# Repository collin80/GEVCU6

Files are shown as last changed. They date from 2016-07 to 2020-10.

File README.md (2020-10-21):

GEVCU
=====

Generalized Electric Vehicle Control Unit

Our website can be found at : http://www.evtv.me

NOTE: This branch is quite old and not really supported at this point. Use the DEV branch of this project if at all possible. It is newer and better supported. Eventually the DEV branch will be merged back into this master branch.

A project to create a fairly Arduino compatible ECU firmware
to interface with various electric vehicle hardware over CANbus
(and possibly other comm channels)

The project now builds in the Arduino IDE. So, use it to compile, send the firmware to the GEVCU hardware, and monitor serial. It all works very nicely.

You will need the following to have any hope of compiling and running the firmware:
- A GEVCU board. This version supports hardware 6.23c and later.
- Arduino IDE 1.5.4 - or later
- due_can library - There is a repo for this under github.com/Collin80
- can_common library - Also under Collin80 repos
- due_rtc library - Also under Collin80
- due_wire library - once again
- DueTimer library - and again
- Microsmooth library (Also in repos: https://github.com/collin80/Microsmooth)
- Adafruit_BLE_SPI library - You need the development branch from my repos: https://github.com/collin80/Adafruit_BLE_SPI/tree/development

All libraries belong in %USERPROFILE%\Documents\Arduino\libraries (Windows) or ~/Arduino/libraries (Linux/Mac).
You will need to remove -master or any other postfixes. Your library folders should be named as above.

The canbus is supposed to be terminated on both ends of the bus. If you are testing with a DMOC and GEVCU then you've got two devices, each on opposing ends of the bus. GEVCU hardware is already terminated internally.

This software is MIT licensed:

Copyright (c) 2014 Collin Kidder, Michael Neuweiler, Charles Galpin, Jack Rickard

Permission is hereby granted, free of charge, to any person obtaining
a copy of this software and associated documentation files (the
"Software"), to deal in the Software without restriction, including
without limitation the rights to use, copy, modify, merge, publish,
distribute, sublicense, and/or sell copies of the Software, and to
permit persons to whom the Software is furnished to do so, subject to
the following conditions:

The above copyright notice and this permission notice shall be included
in all copies or substantial portions of the Software.

THE SOFTWARE IS PROVIDED "AS IS", WITHOUT WARRANTY OF ANY KIND,
EXPRESS OR IMPLIED, INCLUDING BUT NOT LIMITED TO THE WARRANTIES OF
MERCHANTABILITY, FITNESS FOR A PARTICULAR PURPOSE AND NONINFRINGEMENT.
IN NO EVENT SHALL THE AUTHORS OR COPYRIGHT HOLDERS BE LIABLE FOR ANY
CLAIM, DAMAGES OR OTHER LIABILITY, WHETHER IN AN ACTION OF CONTRACT,
TORT OR OTHERWISE, ARISING FROM, OUT OF OR IN CONNECTION WITH THE
SOFTWARE OR THE USE OR OTHER DEALINGS IN THE SOFTWARE.

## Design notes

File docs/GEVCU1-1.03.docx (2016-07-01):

GENERALIZED ELECTRIC VEHICLE CONTROL UNIT

GEVCU

SPECIFICATION

Jack Rickard jack@evtv.me

# BACKGROUND

For 40 years and more, individual tinkerers and innovators have been modifying existing automobiles to electric drive and often building electrically powered vehicles from scratch.

The early “controllers” that evolved to replace simple switching and resistive controls to control the speed of the driver motors were mostly pulse width modulated (PWM) devices to provide an averaged DC signal to a series DC motor. These simple chopper voltage control devices were generally referred to as “controllers” and translated driver input from “controls” such as the accelerator pedal, ignition switch, and brake to this motor driving voltage to control its speed and direction – and consequently the vehicle.

There are of course many other types of motors such as separately excited DC motors, brushless DC motors, permanent magnet motors and AC induction motors. Most of these polyphase motors required 3 phase “inverters” to convert the DC power of the battery pack into three phase drive signals varying the voltage and frequency of the power to the motor to accomplish the same thing.

Most of the DC “controllers” received the inputs directly by wiring from the sensors or controls in the cars.

In recent years, among automobile manufacturers, the use of the Controller Area Network bus protocol has been adopted for many of the items in the automobile, including the internal combustion engine – often called an Engine Control Unit or a Vehicle Control Unit which forms the central “brains” of the car. It is connected to various sensors and controls by wire but communicates to other subsystems of the vehicle such as the instrumentation, ABS system, transmission, environmental system using this CANbus as the common link.

Automakers have eschewed the DC motor in favor of either permanent magnet AC motors or AC induction motors. And the “inverters” developed to drive these were interfaced to this same CANbus model for control input.

Because of the varying nature of the cars, the ECU or VCU would be specifically designed for that vehicle. But the Inverters driving AC motors can be somewhat generalized to work in any car by using CANbus to control them.

The VCU would be specifically designed and software specifically written for that vehicle. This was hardcoded into flash memory and defined the operation of the vehicle. No end user input or options were provided. Firmware updates were accomplished by revising the hard code, recompiling, and having the controller reflashed with the new binaries at the dealership during normal maintenance.

And so thousands of these VCUs could be flashed when built, with the software specific to that particular vehicle.

The VCU would of course be completely inappropriate and non functional in another vehicle make or model.

As many automakers are experimenting with product introductions of plug-in electric vehicles and hybrid gasoline/electric vehicles, many of the components used in these vehicles are becoming available when the cars are salvaged and are recycled through salvage yards and such online services as eBay.

As such, they will become a resource to individual tinkerers and those converting existing cars to electric drive.

But almost all of these components were designed to be controlled by the Vehicle Control Unit that came with the original car.

It would be a serious advantage, to have a more generalized vehicle control unit that allowed some basic configuration allowing these conversions to modify operation of the VCU to accommodate THEIR car without the need to entirely rewrite the software and flash the VCU.

As almost all VCU accomplish the same basic functions, a simple configuration input that does not involve assembly language or C programming to change it would be of substantial utility.

This document describes the design of a Generalized Vehicle Control Unit. The multicontroller hardware will allow connection of the basic sensor set necessary to drive the car such as throttle signals, brake signals, ignition signal, and control the basic common outputs such as brake lights, fuel level, rpm, power usage, while serving in the central role of converting these inputs to CAN messages for the inverter to actually drive the car.

The operation of this device can be modified, within fairly narrow constraints, by a simple configuration “menu” style input that non-programmers can access and make changes to, in order to interface the VCU to the particular car they want to convert.

The initial immediate need for this Generalized Vehicle Control Unit was the acquisition of a significant number of Siemens 1PV5135-4WS14-Z motors and Digital Motor Control (DMOC) 645 units from the liquidation of Azure Dynamics Corporation by EVtv.

This DMOC no longer has control inputs, but is rather designed to respond to CANbus commands solely.

The intent in developing this GEVCU, is to not only allow access to a number of OEM hardware components, but also to transfer the product support function faced by the manufacturers and developers of the Inverter Power Electronics to the GEVCU.

In theory, CANbus message digests for ANY motor inverter could be easily patched into the GEVCU to allow operation of that power inverter without ANY support from the developer of the power electronics.

This should quickly allow the developers of power electronics inverters to provide this equipment to individuals at the same or comparable prices as they do to the OEM automakers, without having to incur additional expense to train and support those users in the use of the product. Training and use becomes a function of using the GEVCU itself.

# HARDWARE DESIGN PHILOSOPHY

GEVCU developers can use any hardware they can build or locate that accommodates the basic sensor inputs and instrumentation outputs described in this document. OPEN SOURCE hardware prototype equipment is preferred for GEVCU development and the software should be designed to operate on an open source prototype system. But it is perfectly acceptable to then design custom hardware from that reference design to reduce costs and eliminate extraneous unused components available in the open source prototype system design.

The hardware must provide:

1. At least one CANbus port capable of CAN 1.0 and 2.0b operation, including both 11 bit and 29 bit identifiers.
2. A sufficient number of analog to digital converter inputs of sufficient resolution to accommodate the sensor inputs described in this document. Vehicle sensors are overwhelmingly based on 0-5V architectures. And so these A/D inputs must accept signals in the 0-5v range, and the device must be able to provide 5v supplies to those sensors in sufficient power levels to not alter the 5v reference level when all such sensors are connected.
3. Digital inputs capable of recognizing on/off signals from the vehicle given in 12v and ground states. Active can be either of active high 12v or active low gnd but active high is the normally preferred method as 12v is normally the enabling signal for other systems such as brake lights.
4. Relay driver outputs. Digital outputs suitable for engaging relays, contactors, and other relay like devices in the vehicle.
5. PWM outputs. Sufficient PWM outputs to drive legacy instrumentation such as tachometers and fuel gages as described in this document.
6. ETHERNET port. It is very important for the end user to be able to modify the operation of this device (configure it) without the need for unique external software programs running on specific operating systems. The user should be able to easily configure this device using any device with an Ethernet connection and an http browser. It is actually completely acceptable to also provide means of configuration using a browser via 802.b/g/n wireless, Bluetooth, or Universal Serial Bus (USB) interfaces.

The overall requirement here is that no special type of computer, operation system, or unique configuration software external to the GEVCU can be required to easily modify GEVCU configuration and operation.

Additionally we seek to AVOID the additional expense in the device of a dedicated display and input devices in the GEVCU hardware itself. Once configured, this hardware would be entirely redundant. Configuration is conceivably a one time or perhaps very infrequent event.

7. Processor power sufficient to perform the GEVCU tasks without delay in vehicle operation or control. This is quite important as many systems shut down without regular updated CAN messages to keep them alive and the results of any inability to make schedule could be catastrophic in a moving vehicle.
8. Popularity and user base. When selecting hardware, recognize the advantage of popular and widely adopted devices with large user base. That user base provides a level of additional support and utility that it forms a serious element of the ultimate value of the GEVCU.
9. Tool chain. Strong preference should be given to devices with simple and free compilers such as the Arduino IDE. An open hardware open software device makes little sense if it requires a $2800 compiler environment to make code changes.

# SOFTWARE DESIGN PHILOSOPHY

The basic software design philosophy is to be an open source, object oriented software design. This is to accommodate a couple of needs for the GEVCU

1. Ability to add contributions from any external source or user that prove effective in practice. Anyone should be able to read, modify, recompile and run the original source code to the GEVCU. As such, it should be open source and use inexpensive or free, widely available tool chains to compile. If they are caught in the act of doing something useful, that improvement can be added to the main trunk of the software development.
2. Ability to add support for additional inverters. Almost all of the available inverters accomplish essentially the same functions and provide essentially the same information. But the specific CAN bus IDs, command structure and data formats vary entirely from one inverter to another.

The GEVCU will be initially developed to support the Azure Dynamics DMOC645 inverter. But the ability to add the specific CAN bus message commands for other inverters, without having to make changes to the main program structure in a modular fashion is very important.

Make a strong effort to isolate the inverter object from the rest of the code, with an eye towards allowing the use of other inverter objects with no changes to the non-inverter object code.

3. Object Oriented C++ code is an obvious choice. Assembly language subroutines where desirable or advantageous are perfectly acceptable.
4. Recognize an inevitable desire to add additional functions to this device quite beyond the initial GEVCU spec. The GEVCU, by virtue of it’s central role in vehicle operation, would be the natural place to go for controlling electrically powered air conditioner compressors, CANbus controlled battery chargers, CANbus controlled Electronic Power Assisted Steering units (EPAS) etc.

# COMPLIANCE

For teams developing GEVCU hardware and/or software, it should be noted that compliance with this specification is ENTIRELY voluntary.

That said, there is a slight motivator you might want to take into consideration. I happen to know that software developers are notoriously averse to actually documenting anything and hardware designers are even worse – they not only don’t document but they can’t remember either. They’ll have to get with Charlie and get back to you later.

On the other hand, if you design TO the GEVCU specification, and when making necessary changes NOT in compliance get those changes incorporated BACK into the spec, you will find an odd resemblance between your newly finished product and my upcoming best selling novel :

# INSTALLATION AND OPERATION OF THE GENERALIZED ELECTRIC VEHICLE CONTROL UNIT.

By Jack Rickard.

See the movie at a theatre near you. Coming this summer.

# PART 1 - INPUTS

# THROTTLE

The throttle or accelerator is undoubtedly the central control input for a controller. This is how we vary the power output of the inverter to the motor, and thus motor speed and torque, and consequently vehicle speed.

There are two broad types of throttles that must be accommodated: legacy throttles and modern dual signal drive by wire throttles found in currently manufactured vehicles.

The legacy throttle most widely used is a simple 5kohm potentiometer linked to a mechanical pedal usually by wire. The controller provides 5v and a reference ground to the two ends of the resistor, and the pickup arm of the potentiometer returns some fraction of that source voltage to the controller as the signal input.

There are also single channel hall-effect throttles available on the market. But their operation is largely identical. 5v and ref gnd is provided to them, and they return some value between 0 and 5v based on position.

Modern drive by wire throttles used in vehicles today use the same 5v and ref gnd input, but they will provide TWO signal inputs to the controller. These are often two signals of different scale: ie. 0.5 to 4.5 and 1.2 to 3.2. Or they might be inverse function where one signal is 1-4v while the other is 4-1v. In some cases they can be both differing in scale and direction.

These throttles are generally designed for safety in that the controller is suppose to compare the two signals, which have a known relationship, and if the two signals do not correspond, the assumption is that one or both are faulty. As a result, the controller reduces all motor torque and speed commands to zero. This prevents a runaway situation resulting from loss of ground, or loss of 5v, or other wiring incident or component failure.

PINS: 1. 5vdc supply voltage 50 ma out to sensor

2. Signal 0-5vdc ADC input ADC

3. Optional sanity check voltage ADC input

3. Reference return – ground out to sensor

CONFIGURATION VARIABLES:

THROTMIN: This parameter sets the minimum voltage where the throttle is considered active. Voltages below this value are read as no throttle input.

Example: 0.80 would indicate 0.80v

THROTMAX: This parameter sets the maximum voltage where the throttle is considered active. Voltages above this value are read as no throttle input.

Example: 4.75 would indicate 4.75v

THROTNOTMIN: This parameter sets the minimum voltage where the optional sanity check throttle input is considered active. Voltages below this value are read as no throttle input.

Example: 1.20 would indicate 1.20v

THROTNOTMAX: This parameter sets the maximum voltage where the optional sanity check throttle input is considered active. Voltages above this value are read as no throttle input.

Example: 3.60 would indicate 3.60v

The sanity check is NOT performed if either THROTNOTMIN or THROTNOTMAX is zero. If they are non zero, the percentage of maximum throttle signal between THROTNOTMIN and THROTNOTMAX is calculated. Also the percentage of maximium throttle signal between THROTMIN and THROTMAX is calculated. The two percentages are compared, and if not within 5% of each other, a fault is thrown and CANbus signals generated to put inverter at zero torque and zerospeed.

Note that this calculation MUST handle the case where THROTNOTMIN is a larger positive voltage value than THROTNOTMAX – the inverse case.

THROTREGEN: Voltages between this value and THROTMIN result in a linear increase in regenerative braking, with maximum regenerative braking established by THROTMAXREGEN at the THROTMIN voltage and essentially 0 percent of MAXREGEN at the THROTREGEN point.

Example: 1.50 indicates 1.50v

Zero regenerative braking at 1.50 v increasing to THROTMAXREGEN at THROTMIN.

In this way, as you begin easing off the throttle through the deadband, at THROTREGEN regenerative braking is still zero. As the voltage falls, regenerative braking INCREASES to the point set by THROTMAXREGEN when the voltage falls to THROTMIN. And so the further we remove the throttle, the greater the amount of regenerative torque is applied.

THROTFWD: Typically a small voltage value above THROTREGEN establishing a “dead band” between the THROTREGEN point and the THROTFWD point.

Example: 1.8v

In this example, from THROTREGEN (1.50v_ to THROTFWD (1.8v) is the deadband or coast zone. NO torque or speed commands are provided to the inverter if throttle input is both valid and in this band, allowing the motor and the vehicle to free roll.

The area between THROTFWD and THROTMAX defines the region of forward acceleration with the minimum torque/speed values occurring at THROTFWD and the maximum torque and speed values at THROTMAX.

THROTMAP: This variable represents a voltage between and THROTMAX where a 50% torque and speed level is defined.

A linear increase of torque and speed is mapped between THROTFWD and THROTMAP with 50% of available torque and speed occurring at THROTMAP.

A linear increase in torque and speed is also mapped between THROTMAP and THROT MAX representing the remaining 50% of available torque.

This entered value is then used to warp the throttle curve. For example:

THROTFWD: 1.80v

THROTMAP: 3.80v

THROTMAX: 4.65v

It can be seen that the first 50% of available torque is mapped between 1.80 and 3.80v while the second 50% of available torque is mapped linearly between 3.80v and 4.65v.

In this way, low speed handling and maneuvering has greater resolution spread across 2.00v of the throttle range, while less resolution is provided across the upper 0.85v. Higher resolution is desired at take off, or while parking, or reversing, while it is generally not needed in going from 50% to full power when we are basically just wanting a big increase in power. THROTMAP can be used to slide this point between those two extremes.

THROTMAXREGEN: This variable defines the percentage of available maximum torque that is available for regenerative braking at the THROTMIN point.

Note that a value of 0 indicates no regenerative braking at all using the throttle.

MAXREGEN: This variable defines the percentage of available maximum torque that is ever available for regenerative braking.

MAXTORQ: This defines the maximum torque available for any purpose.

# BRAKE

You might note that the throttle input also has provisions for regenerative braking. The brake signal does as well. We would assume that the vehicle has a fully functional normal brake system, and that it also has a brake switch used to turn on the brake lights.

Regenerative braking is normally a function of the brake input.

PINS: 1. 5vdc supply voltage 50 ma out to sensor

2. Brake pressure sensor signal 0-5vdc input ADC

3. Reference return – ground out to sensor

4. Brake light input – 0 or 12v digital input

CONFIGURATION VARIABLES:

BRAKEMIN: This parameter sets the minimum voltage where the brake sensor is considered active. Voltages below this value are read as no brake input.

BRAKEMAX: The maximum voltage logic will read as valid brake pressure sensor input. Voltages above BRAKEMAX are read as no brake input.

BRAKEMAXREGEN. This is a value from 0 to 100 representing the percentage of MAXTORQ that can be applied during regenerative braking.

The actual value of regenerative braking during a braking event is a linear value between MAXTHROTREGEN at BRAKEMIN and BRAKEMAXREGEN at BRAKE MAX.

In this way, when you remove your foot from the throttle, the regenerative level is set at the value of MAXTHROTREGEN. When your foot first applies to the brake, that SAME level of REGEN is maintained. As more brake pressure is applied, the regenerative braking torque increases until it reaches BRAKEMAXREGEN at the BRAKEMAX point.

Note that by setting BRAKEMAX to some voltage LESS than the actual maximum voltage provided by the sensor, you can slide the regenerative braking zone toward the very lightest application of brake, and as you continue to press the pedal, regenerative braking ceases and the normal brake system takes over. This can be effective to get maxium regenerative braking effect before the normal disk or drum brakes begin to become effective.

Normally, NO regenerative braking will be provided without a secondary signal from the brake light input. This is a secondary input from a separate source used to enable regenerative braking.

BRAKREGENRAMPTIME. This is a value between 0 and 255 representing the number of hundredths of a second to use to ramp from THROTMAXREGEN to BRAKEMAXREGEN if the brake sensor input value is below BRAKEMIN but the brake light input is active.

In this event, we assume we are NOT USING a brake pressure tranducer input at all. But we do have an active brake light switch signal. The regenerative braking will gradually increase from THROTMAXREGEN to BRAKEMAXREGEN in linear fashion across the entered time value with a max time of 2.5seconds.

This is counterintuitive and we’ve actually seen inverters with this function coded in backwards. But it doesn’t work well when braking.

In the event we are not using regen on the throttle, and want to use it on the brakes, but have no transducer, the regenerative braking will gradually be applied when we step on the brake pedal and steadily increase. If we get too much braking, we simply remove our foot from the brake. Regen goes to zero. We can REAPPLY the brake pedal and again regenerative braking starts to increase. In practice, this feels like you are pumping the brakes.

# REGENERATIVE BRAKING ADJUST

Regenerative braking is a highly subjective “feel” issue. It would be very nice to provide a knob on an electric vehicle where the driver could manually adjust the regen level just by turning the knob.

PINS: 1. 5vdc supply voltage 50 ma out to sensor

2. Regenerative brake adjust signal 0-5vdc input ADC

3. Reference return – ground out to sensor

CONFIGURATION VARIABLES:

REGENSCALE. This variable is set between 0 and 100% based on the voltage read on the regenerative braking adjust signal input. Voltages below 1v set this value to 0. Voltages between 1 and 4v are converted to a decimal value less than 1 indicating the percentage of regen desired. Voltages above 4 are read as 4.

THROTMAXREGEN and BRAKEMAXREGEN are scaled by multiplying the values entered on the configuration screen by REGENSCALE.

As a result, potentiometer settings resulting in an input voltage less than 1 effectively disables regenerative braking. Voltages between 1 and 5 scale regenerative braking.

# IGNITION

The switched ignition 12v from the vehicle is used to turn on the GEVCU. It is also the source of power for the GEVCU.

PINS: 1. 12vdc supply voltage in from vehicle ignition switch.

CONFIGURATION VARIABLES: None.

# FORWARD

The internal DIRECTION variable should be used to indicate forward (1), reverse (2), or neutral (0) operation. IF REVERSE and NEUTRAL input pins are inactive, set DIRECTION to 1.

PINS: 1. 12vdc digital input.

CONFIGURATION VARIABLES:

ACTIVEHIGH. This single configuration variable determines if input pins are active high (greater than 4 volts) or active low (less than 3 volts). All digital input pins should be able to endure voltage values up to 15v which may occur in vehicles. This variable applies to ALL digital input pins on the VCU.

# REVERSE

The internal DIRECTION variable should be used to indicate forward (1), reverse (2), or neutral (0) operation. IF FORWARD and NEUTRAL input pins are inactive, set DIRECTION to 2.

PINS: 1. 12vdc digital input.

CONFIGURATION VARIABLES:

ACTIVEHIGH. This single configuration variable determines if input pins are active high (greater than 4 volts) or active low (less than 3 volts). All digital input pins should be able to endure voltage values up to 15v which may occur in vehicles. This variable applies to ALL digital input pins on the VCU.

# NEUTRAL

The internal DIRECTION variable should be used to indicate forward (1), reverse (2), or neutral (0) operation. IF FORWARD and REVERSE input pins are inactive, set DIRECTION to 0.

PINS: 1. 12vdc digital input.

CONFIGURATION VARIABLES:

ACTIVEHIGH. This single configuration variable determines if input pins are active high (greater than 4 volts) or active low (less than 3 volts). All digital input pins should be able to endure voltage values up to 15v which may occur in vehicles. This variable applies to ALL digital input pins on the VCU.

# GENERAL ENABLE

This input can be used to enable the VCU operation. If active, AND the GENERAL DISABLE input is INACTIVE, sets internal variable ENABLE to 1. This internal variable is used to determine whether to allow drive speed and torque commands to the inverter. If this input goes inactive, the ENABLE variable is set to 0.

PINS: 1. 12vdc digital input.

CONFIGURATION VARIABLES:

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

# GENERAL DISABLE

This input can be used to enable the VCU operation. If any of these three input pins go active, sets internal variable ENABLE to 0 regardless of GENERAL ENABLE input. This internal variable is used to determine whether to allow drive speed and torque commands to the inverter. If this input goes inactive, NO change is made to the ENABLE variable and we rely on the general enable input to reset ENABLE to 1.

PINS: 1. 12vdc digital input – DISABLE 1.

2. 12vdc digital input - DISABLE 2

3. 12vdc digital input - DISABLE 3

CONFIGURATION VARIABLES:

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

# LIMP MODE

This input is used to force an immediate reduction in power available via speed and torque command. All speed and torque commands are scaled by the LIMPSCALE variable.

PINS: 1. 12vdc digital input.

CONFIGURATION VARIABLES:

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

LIMPSCALE. 0-100. This configuration variable is used as a multiplier for ALL torque and speed commands to the vehicle. The default value is 100 indicating full power Scotty. Lower values of course reduce output power to the percentage indicated in this variable. The variable is applied ONLY when the LIMPMODE input is active.

# OUTPUTS

# CONTROLLER STATUS

This output is used to indicate status of the GEVCU. If it is turned ON and left on in a steady state, this indicates the GEVCU has powered up, established communications with the inverter, and passed all internal operational checks.

PINS: 1. Digital output LED driver.

CONFIGURATION VARIABLES: None

If this LED is flashed 1 to 9 times, followed by off for two seconds, followed by another series of flashes 1 to 9, this indicates a fault code. Fault codes can be, 11 through 19, 21 through 29, 31 through 39 etc. up to 99.

Fault Code 99 is defined as FAULT - NO FAULT CODE PROVIDED.

Fault Code 11 is defined as NO INVERTER COMMUNICATIONS.

Any developer can register a fault code and we’ll add it. First come, first served.

# PRECHARGE RELAY OUTPUT

This output is used to close a precharge relay, applying high voltage to the Inverter through a precharge resistor. icates the GEVCU has powered up, established communications with the inverter, and passed all internal operational checks.

PINS: 1. Digital output 12v RELAY driver. 500ma

CONFIGURATION VARIABLES:

PRECHARGERELAY: This variable is set by the user using a checkbox or radio button. The variable is set to 1 if selected and 0 if not indicating the need for a precharge relay output on power up.

If 1, a digital output is provided as part of the startup sequence. If the digital output does not provide sufficient current, an external MOSFET may be required to drive the relay.

Many inverters such as Rinehart do their own precharge management. The DMOC 645 does not. So this will always be an optional output configurable by the user.

# CONTACTOR RELAY OUTPUT

This output is used to close a contactor high current relay, applying high voltage to the Inverter directly. Most contactors can experience an initial closing current requirement of up to 1.5 amps and subsequently settle to 300 ma or so.

PINS: 1. Digital output 12v RELAY driver. 1.5 amps.

CONFIGURATION VARIABLES:

CONTACTOR: This variable is set by the user using a checkbox or radio button. The variable is set to 1 if selected and 0 if not indicating the need for a contactor relay output on power up.

If 1, a digital output is provided as part of the startup 3 seconds after the PRECHARGERELAY output. If the digital output does not provide sufficient current, an external MOSFET may be required to drive the contactor.

# REVERSE LIGHT RELAY OUTPUT

This output is used to close a relay, applying 12v to the reverse lights of the vehicle. This will normally be done by the transmission, but on certain vehicles without transmission, could be reversed using the REVERSE input to reverse the motor speed and torque commands. This output is always available and set active whenever the internal DIRECTION variable is set to 0

PINS: 1. Digital output 12v RELAY driver. 500 ma.

CONFIGURATION VARIABLES: None

If the digital output does not provide sufficient current, an external MOSFET may be required to drive the 12v relay

# COOLING RELAY OUTPUT

This output is used to close a relay, applying 12v to drive cooling pumps or fans or both. This is set to active whenever CANbus status signals are received from the inverter indicating a motor or inverter temperature reaching a certain level.

PINS: 1. Digital output 12v RELAY driver. 500 ma.

CONFIGURATION VARIABLES:

COOLINGTEMP: 0-300

This configuration variable allows the user to enter the temperature of either motor or inverter where the coolant output goes active. Zero to 300C.

# MOTOR TEMPERATURE OUTPUT

This is a Pulse Width Modulated output representing motor temperature. It can be used to drive a temperature gage. It will be active only if motor temperature is available from inverter via CAN status message.

PINS: 1. 5v PWM output.

CONFIGURATION VARIABLES:

MOTORMINTEMP: 0-300

This variable allows user to enter a motor temperature corresponding to the lowest reading on their gage and nominally a PWM value of 0%.

MOTORMAXTEMP: 0-300

This variable allows the user to enter a motor temperature in degrees centigrade to correspond with a PWM output of 100%.

# INVERTER TEMPERATURE OUTPUT

This is a Pulse Width Modulated output representing inverter temperature. It can be used to drive a temperature gage. It will be active only if inverter temperature is available from inverter via CAN status message.

PINS: 1. 5v PWM output.

CONFIGURATION VARIABLES:

INVMINTEMP: 0-300

This variable allows user to enter an inverter temperature corresponding to a PWM value of 0%.

INVMAXTEMP: 0-300

This variable allows the user to enter an inverter temperature in degrees centigrade to correspond with a PWM output of 100%.

Output should of course be scaled from INVMINTEMP to INVMAXTEMP 0 to 100%. Temperatures above max will be shown at 100% and temperatures below min will be shown at 0% but of course.

# RPM OUTPUT

This is a pulsed digital output that can be used with a 12v opto isolator to drive a common tachometer. RPM from Inverter CAN status message is converted to a series of digital pulses..

PINS: 1. pulsed digital output.

CONFIGURATION VARIABLES:

TACHPPT:

This variable allows user to enter the number of pulses to output per turn PPT corresponding to their tachometer. The output is scaled to a frequency representing this number of pulses per rpm.

Example: 6000 rpm = 100 rps x 4ppt = 400Hz

# BATTERY CURRENT OUTPUT

This is a pulsed digital output that can be used with a 12v opto isolator to drive a common tachometer. Battery current from Inverter CAN status message is converted to a series of digital pulses..

PINS: 1. pulsed digital output.

CONFIGURATION VARIABLES:

AMPPPT:

This variable allows user to enter the number of pulses to output per turn PPT corresponding to their tachometer. The output is scaled to a frequency representing this number of pulses per rpm.

Example: 600 amp = 100 rps x 4ppt = 400Hz

In this case 600 amps of battery current will appear on a tachometer as 6000 rpm if it is a 4 pulse per turn tachometer.

# OTHER CONFIGURATION VARIABLES

MAX RPM – maximum RPM controller should command to inverter.

MAX TORQUE – maximum torque controller should command to inverter.

MAX REGEN – maximum regenerative braking torque controller should command.

# GEVCU STATUS DISPLAY HTML

### Battery voltage _____v

### Battery current ______A

### Battery power ______kW

### Motor temp: ______C

### Inverter temp: ______ C

### Motor Torque: ______ %

### Motor Speed: ______rpm

### Power used since start: _____kWh

### BUTTON – GEVCU SETUP

# GEVCU CONFIGURATION

# GENERAL LIMITS

### MAXRPM (1000-10000) ______rpm

### MAXTORQUE (0-100): ______%

### ACTIVEHIGH [ ] yes [ ] no

### LIMPSCALE(0-100) ____%

# THROTTLE/ACCELERATOR

### THROTMIN (0.00-5.00v) : _________v

### THROTREGEN (0.00-5.00): _______v

### THROTFWD(0.00-5.00): _______v

### THROTMAP(0.00-5.00): _______v

### THROTMAX(0.00-5.00): _______v

### THROTNOTMIN(0.00-5.00): _______v

### THROTNOTMAX(0.00-5.00): _______v

### 0.00==THROTMIN==THROTREGEN==THROTFWD==THROTMAP=THROTMAX ==5.00

### 0.00==THROTNOTMIN=============================THROTNOTMAX-====5.00

\

# BRAKE INPUT

### BRAKEMIN (0.00-5.00v) : _________v

### BRAKEMAX (0.00-5.00): _______v

# REGENERATIVE BRAKING

### MAXREGEN (0-100): _____%

### REGENSCALE (0-100): _____%

### THROTMAXREGEN (0-100) ____%

### BRAKEMAXREGEN (0-100) ____%

### BRAKEREGENRAMPTIME(0-255): _______seconds

# OUTPUTS

### PRECHARGE RELAY OUTPUT [ ] yes [ ] no

### CONTACTOR OUTPUT [ ] yes [ ] no

### COOLING OUTPUT(0-300): _______centigrade

### MOTORMINTEMP(0-300): _______centigrade

### MOTORMAXTEMP(0-300): _______centigrade

### INVERTERMINTEMP(0-300): _______centigrade

### INVERTERMAXTEMP(0-300): _______centigrade

### TACHPPT (0-8) ____ ppt

### AMPPPT (0-8) ____ ppt

### BUTTON – ACCEPT CONFIG CHANGES

### BUTTON – GEVCU STATUS

# GEVCU CONFIGURATION TOOLTIPS

Tooltips that may be incorporated into GEVCU configuration html form.

# GENERAL LIMITS

### MAXRPM (1000-10000) ______rpm

The maximum motor speed the GEVCU will call for or allow. If this limit is reported by the Inverter, motor torque, speed or both will be reduced by CANbus command.

### MAXTORQUE (0-100): ______%

The maximum motor torque that can be commanded by CANbus

### ACTIVEHIGH [ ] yes [ ] no

Yes indicates activation of digital inputs will be read with 12v applied to pin. No indicates ACTIVE LOW with ground applied to pin read as ACTIVE.

### LIMPSCALE(0-100) ____%

Percent of maximum torque and speed allowed when LIMPMODE input is active.

# THROTTLE/ACCELERATOR

### THROTMIN (0.00-5.00v) : _________v

Values below this voltage are read as a fault on the accelerator input.

### THROTREGEN (0.00-5.00): _______v

Regenerative braking is linearly increased from this voltage/pedal position DOWN to THROTMIN.

### THROTFWD(0.00-5.00): _______v

Region between THROTREGEN and THROTFORWD defines dead band or COAST area of throttle. Torque and speed are linearly increased from this point to THROTMAX.

### THROTMAP(0.00-5.00): _______v

Defines point between THROTFWD and THROTMAX where 50% of available torque/speed is available. By setting this higher, better low speed resolution/control.

### THROTMAX(0.00-5.00): _______v

Voltages above this are read as throttle faults.

### THROTNOTMIN(0.00-5.00): _______v

Minimum voltage of second throttle input. 0 indicates no input. Any other value establishes ratio to THROTMIN

### THROTNOTMAX(0.00-5.00): _______v

Maximum voltage of second throttle input. 0 disables second throttle input. Any other value corresponds to THROTMAX. It is acceptable for THROTNOTMIN to be greater than THROTNOTMAX, indicating a reversed linear input for comparison to the main throttle input.

### 0.00==THROTMIN==THROTREGEN==THROTFWD==THROTMAP=THROTMAX ==5.00

### 0.00==THROTNOTMIN=============================THROTNOTMAX-====5.00

\

# BRAKE INPUT

### BRAKEMIN (0.00-5.00v) : _________v

Voltages below BRAKEMIN are read as brake sensor faults. Regenerative braking is linearly ramped between BRAKEMIN and BRAKEMAX in most instances.

### BRAKEMAX (0.00-5.00): _______v

Voltages above BRAKEMAX are read as brake sensor faults. Regenerative braking is linearly ramped between BRAKEMIN and BRAKEMAX in most instances.

# REGENERATIVE BRAKING

### MAXREGEN (0-100): _____%

Percentage of MAXTORQUE that can be applied as regenerative braking.

### REGENSCALE (0-100): _____%

MAXREGEN, THROTMAXREGEN, and BRAKEMAXREGEN are all reduced identically if this value is less than 100.

### BRAKEMAXREGEN (0-100) ____%a

Percent of MAXREGEN allowed for braking

### BRAKEREGENRAMPTIME(0-255): _______seconds

Number of seconds to ramp from THROTTREGEN to BRAKEMAXREGEN in the event there is no brake pressure sensor input and we are doing regenerative braking from the brake light input only.

# OUTPUTS

### PRECHARGE RELAY OUTPUT [ ] yes [ ] no

Yes if you want a relay drive signal to engage an external relay. No if not.

### CONTACTOR OUTPUT [ ] yes [ ] no

Yes if you want a 1.5amp relay output to engage high voltage contactor relay

### COOLING OUTPUT(0-300): _______centigrade

Temperature of motor or inverter where a COOLING relay output is provided.

### MOTORMINTEMP(0-300): _______centigrade

Minimum motor temperature corresponding to 1% PWM output on MOTOR TEMP output.

### MOTORMAXTEMP(0-300): _______centigrade

Motor temperature corresponding to 99% PWM output on MOTOR TEMP .

### INVERTERMINTEMP(0-300): _______centigrade

Minimum reported inverter temperature corresponding to 1% PWM output on INVERTER TEMP output.

### INVERTERMAXTEMP(0-300): _______centigrade

Inverter temperature corresponding to 99% PWM output on INVERTER TEMP .

### TACHPPT (0-8) ____ ppt

Pulses per turn for dashboard tachometer to read RPM output of GEVCU

### AMPPPT (0-8) ____ ppt

Pulses per turn for dashboard tachometer to read amperes in hundreds on tachometer thousands of RPM gage.

### BUTTON – ACCEPT CONFIG CHANGES

Sends these configuration changes to GEVCU

### BUTTON – STATUS

Causes GEVCU to display current status screen.

# GEVCU EEPROM MAPPING

This section describes the mapping and location of certain configuration variables necessary for the Generalized Vehicle Control Unit. When an end user sends the HTML form containing configuration items, those items will be extracted from the HTML and stored in the Macchina EEPROM so they are persistent between operations. The program can then retrieve these configuration variabales from EEPROM as part of the basic initialization procedure.

1000 unsigned int MAXRPM (1000-10000) ______rpm

1002 byte MAXTORQUE (0-100): ______%

1003 bool ACTIVEHIGH [ ] yes [ ] no

1004 byte LIMPSCALE(0-100) ____%

1005 unsigned int THROTMIN (0-500 /0.00-5.00v) : _________v

1007 unsigned int THROTREGEN 0-500(0.00-5.00): _______v

1009 unsigned int THROTFWD 0-500(0.00-5.00): _______v

1011 unsigned int THROTMAP 0-500(0.00-5.00): _______v

1013 unsigned int THROTMAX 0-500 (0.00-5.00): _______v

1015 unsigned int THROTNOTMIN 0-500(0.00-5.00): _______v

1017 unsigned int THROTNOTMAX0-500(0.00-5.00): _______v

1019 unsigned int BRAKEMIN 0-500(0.00-5.00v) : _________v

1021 unsigned int BRAKEMAX 0-500(0.00-5.00): _______v

1023 byte MAXREGEN (0-100): _____%

1024 byte REGENSCALE (0-100): _____%

1025 byte THROTMAXREGEN (0-100) ____%

1026 byte BRAKEMAXREGEN (0-100) ____%

1027 byte BRAKEREGENRAMPTIME(0-255): _______seconds

1028 bool PRECHARGE RELAY OUTPUT [ ] yes [ ] no

1029 bool CONTACTOR OUTPUT [ ] yes [ ] no

1030 unsigned int COOLING OUTPUT(0-300): _______centigrade

1032 unsigned int MOTORMINTEMP(0-300): _______centigrade

1034 unsigned int MOTORMAXTEMP(0-300): _______centigrade

1036 unsigned int INVERTERMINTEMP(0-300): _______centigrade

1038 unsigned int INVERTERMAXTEMP(0-300): _______centigrade

1040 byte TACHPPT (0-8) ____ ppt

1041 byte AMPPPT (0-8) ____ ppt

GEVCU Specification 1.03 February 7, 2013

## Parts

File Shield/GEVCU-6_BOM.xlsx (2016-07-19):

Qty | Value | Device | Part Number | Vendor | Parts | Picture
5 | GREEN | LED0805 | 645-598-8170-107F | Mouser | +3.3V, +5V, +12V, LED, USB2
19 | 10u | C-USC0805 | 80-C0805C106K8P | Mouser | C1, C9, C11, C12, C22, C30, C33, C36, C39, C42, C53, C57, C66, C80, C82, C83, C85, C92, C94
55 | 0.1u | C-USC0805 | 80-C0805C104J8R | Mouser | C2, C3, C4, C5, C6, C7, C8, C10, C13, C14, C15, C16, C17, C18, C19, C20, C21, C29, C31, C32, C34, C35, C37, C38, C40, C41, C43, C44, C45, C46, C49, C52, C55, C56, C58, C59, C60, C61, C64, C65, C67, C68, C70, C71, C73, C76, C79, C81, C84, C86, C87, C90, C91, C95, C97
3 | 22p | C-USC1206 | 77-VJ1206A220JXQCBC | Mouser | C23, C24, C54
3 | 22p | C-USC0805 | 581-0805ZA220JAT2A | Mouser | C25, C26, C27
1 | 0.01u | C-USC0805 | 77-VJ0805A103KXQTBC | Mouser | C28
2 | 0.033u | C-USC0805 | 77-VJ0805Y333KBABC31 | Mouser | C50, C51
6 | 4.7u | C-USC0805 | 810-CGA4J1X7R1E475MA | Mouser | C47, C48, C62, C63, C88, C89
2 | 47n | C-USC0805 | 581-0805ZC473JAZ2A | Mouser | C69, C72
1 | 100u | CPOL-USE2.5-6 | 667-EEU-FM1E101 | Mouser | C74
2 | 1u | C-USC0805 | 80-C0805C105J3RACTU | Mouser | C75, C93
1 | 2u | C-USC0805 | 810-CGA4J1X7R1V225K | Mouser | C77
1 | 0.01u 2kv | C-USC1812 | 605-202S43W103KV4E | Mouser | C78
1 | 680u | CPOL-US5-10.5 | 661-EKZM250E681MJ16S | Mouser | C96
8 | MBR0520LT | MBR0520LT | 512-MBR0520L | Mouser | D1, D2, D3, D4, D5, D6, D7, D8
1 | B360B-13-F | DIODE-SMB | 621-B360B-F | Mouser | D9
7 | BAS70XY | BAS70XY | 771-BAS70XY115 | Mouser | D10, D11, D12, D13, D14, D20, D36
2 | PUCHBUTTON | PUSHBUTTON | 688-SKQYAB | Mouser | ERASE, RESET
2 | ISO1050DW | ISO1050 | 595-ISO1050DW | Mouser | IC9, IC10
2 | 1x18HEADER | PINHD_1x18 | 517-929850-01-18-RA | Mouser | JP1, JP2
13 | MH2029-300Y | WE-CBF_0805 | 652-MH2029-300Y | Mouser | L1, L2, L3, L4, L5, L6, L7, L8, L9, L10, L11, L12, L13
2 | ILD213 | ILD213 | 782-ILD213T | Mouser | OK1, OK2
9 | 2.5A | PTC1812 | 576-1812L150/12DR | Mouser | PTC, PTC0, PTC1, PTC2, PTC3, PTC4, PTC5, PTC6, PTC7
5 | 100k | R-US_R0805 | 71-CRCW0805J-100K-E3 | Mouser | R1, R24, R28, R29, R30
2 | 39R 1% | R-US_R0805 | 71-CRCW0805-39 | Mouser | R2, R3
1 | 6k8 1% | R-US_R0805 | 71-CRCW0805-6.8K-E3 | Mouser | R4
2 | 402R | R-US_R0805 | 71-CRCW0805-402-E3 | Mouser | R5, R58
8 | 10R | R-US_R0805 | 667-ERJ-6GEYJ100V | Mouser | R6, R7, R8, R9, R74, R75, R76, R77
13 | 10k | R-US_R0805 | 667-ERJ-6GEYJ103V | Mouser | R27, R42, R43, R48, R49, R66, R67, R68, R69, R70, R71, R72, R73
4 | 14k 0.1% Thin Film | R-US_R0805 | 667-ERA-6AEB1402V | Mouser | R10, R14, R17, R21
10 | 1k | R-US_R0805 | 71-RCG08051K00JNEA | Mouser | R44, R45, R46, R47, R50, R51, R52, R53, R57, R65
5 | 1k 0.1% Thin film | R-US_R0805 | 667-ERA-6AEB102V | Mouser | R11, R13, R15, R18, R20
2 | 1M 0.1% Thin Film (300V) | R-US_R1206 | 279-CPF1206B1M0E1 | Mouser | R22, R26
2 | 0 Ohm Thin Film | R-US_R0805 | 603-AF0805JR-070RL | Mouser | R12, R19
1 | 750R 0.1% Thin Film | R-US_R0805 | 667-ERA-6AEB751V | Mouser | R16
2 | 1.5k 0.1% Thin Film | R-US_R0805 | 279-CPF0805B1K5E | Mouser | R23, R25
4 | 60R | R-US_R0805 | 667-ERJ-P06D60R4V | Mouser | R38, R39, R40, R41
2 | 4.7k | R-US_R0805 | 71-CRCW0805J-4.7K-E3 | Mouser | R54, R55
1 | 3k3 | R-US_R0805 | 660-RK73G2ATTD3301F | Mouser | R56
8 | NMOSSOT223 | NMOSSOT223 | 726-BSP295H6327XTSA1 | Mouser | T2, T4, T5, T6, T7, T8, T10, T12
1 | SMBJ15A-TR | SUPPRESSOR_SMB | 511-SMBJ15A | Mouser | TVS
1 | CINCON5V | Tracor | TMR 6-2411WI | Mouser | U$1
1 | 581_01_48_005_S | 581_01_48_005_S | 581-01-48-005 | Mouser | U$2
1 | ASE | ASE | 788-8103AI233E-4.0X | Mouser | U$3
1 | ATSAM3X8EA-AU | ATSAM3X | 556-ATSAM3X8EA-AU | Mouser | U1
4 | ADUM3221BRZ | ADUM3221 | 584-ADUM3221BRZ | Mouser | U3, U4, U5, U6
1 | M24M02-DRMN6TP | EEPROM | 511-M24M02-DRMN6TP | Mouser | U7
1 | TRACO | TRACO | TEL5-1210 | Powergate | U8
1 | TSR-1 | TSR-1 | TSR1-2450 | Powergate | U9
1 | LM1117 | LM1117 | 926-LM1117IMPX33NOPB | Mouser | U10
3 | ADE7913 | ADE7913 | 584-ADE7913ARIZ | Mouser | U11, U12, U24
1 | PN61729-S | PN61729 | 292304-1 | Mouser | X1
1 | 12MHz | CRYSTAL-3.2x2.5 | 520-120-20-33-CKMT | Mouser | Y1
1 | 32.768Khz | 32.768Khz | 732-FC135-32.76KAAC3 | Mouser | Y1
1 | 1SMB5929BT3G | ZENER-DIODESMB | 863-1SMB5929BT3G | Mouser | ZEN
1 | 2x10 Header | 2x10 1.27mm Header | 855-M50-3500542 | Mouser | JTAG
Parts not placed onto PCB:
48 | 18ga pins for cinch plug |  | 538-425-00-00-873 | Mouser |  |  | 0.9
1 | 30 pin plug for 48 pin enclosure |  | 538-581-01-30-029 | Mouser |  |  | 59
1 | 18 pin plug for 48 pin enclosure |  | 538-581-01-18-023 | Mouser |  |  | 55
1 | MODICE Enclosure |  | 538-581-01-30-043 | Mouser |  |  | 98

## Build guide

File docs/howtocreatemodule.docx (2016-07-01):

# GEVCU

Generalized Electric Vehicle Control Unit

# Programmer Checklist

# For Adding Object Modules to the

# GEVCU Software

The Generalized Electric Vehicle Control Unit software is open source and object oriented. It was originally developed to control the Azure Dynamics model 645 Digital Motor Controller (DMOC) – a 3-phase inverter/controller used with the Siemens 1PV5134 motor on the Azure Dynamics eTransit Connect.

The DMOC645 was CAN controlled and did not feature any inputs for throttle, brake or other inputs and outputs. The eTransit Connect Vehicle Control Unit (VCU) performed that duty. Lacking the VCU, we had to develop a VCU from scratch capable of providing the necessary CAN messages to the DMOC645 to in turn control the motor.

The concept of a GENERALIZED VCU specifically for electric vehicles derived from the many different types of cars that would be converted to electric drive using this drive system. But from the beginning we saw the need to drive other types of controller/inverters and indeed interact with other devices such as chargers, DC-DC converters, and battery management systems.

So a central tenet of the GEVCU was a very object oriented approach that would easily allow the addition of new classes and new objects to accommodate different equipment. The goal of course to limit software changes to just the additional object added to accommodate the new equipment.

Some wins and some losses. Indeed GEVCU now supports the BRUSA drive train, the CODA/UQM drive train, and more are envisioned and already a series of chargers, BMS, and other devices have been added.

But along the way, we encountered several targets of opportunity that were just two good to pass on, that tend to complicate the easy addition of object modules.

CREATE OBJECT MODULE

TASKING AND PRIORITIES.

PERSISTENT CONFIGURATION STORAGE

MULTIPLE DEVICES ON CAN

# CREATING AN OBJECT MODULE

You create an object module basically by adding a .cpp and .h file to the program set defining your object module. The best way is to copy one from a similar device. If you are doing an object module for a motor controller, a good start would be to copy and rename the DMOC645 motor controller object module held in DmocMotorController.cpp and DmocMotorController.h

Let’s call the new module EVIC and we’ll rename the copied files EVIC.cpp and EVIC.h.

To add these to the program, you basically do two things.

1. Add an include for EVIC.h in the GEVCU.h header file.

#include "EVIC.h"

2. Add a createObjects entry in the main program file GEVCU.ino

void createObjects() {

PotThrottle *paccelerator = new PotThrottle();

CanThrottle *caccelerator = new CanThrottle();

PotBrake *pbrake = new PotBrake();

CanBrake *cbrake = new CanBrake();

DmocMotorController *dmotorController = new DmocMotorController();

CodaMotorController *cmotorController = new CodaMotorController();

DCDCController *dcdcController = new DCDCController();

BrusaMotorController *bmotorController = new BrusaMotorController();

ThinkBatteryManager *BMS = new ThinkBatteryManager();

ELM327Emu *emu = new ELM327Emu();

ICHIPWIFI *iChip = new ICHIPWIFI();

EVIC *eVIC = new EVIC();}

Here, we instantiated the object eVIC of type EVIC as a new instance of EVIC().

Our eVIC object is now part of the program and enjoys all the rights and privileges of other objects of the program.

Note that most objects you will create will actually be child objects of more generalized parent objects. A motor controller object, for example, usually inherits from MotorController and from CanHandler. Much of the basic work common to all motor controllers is already done for you in the parent and standard variables are already there for you to update from your own specific code. You also generally must inherit from CanHandler to be able to catch and send CAN messages in your object.

So you will find something like this in your .h file.

class EVIC: public Device, CanObserver {

public:

Here, in EVIC.h, we are defining a new class EVIC which inherits from the generic Device class but also from CanObserver. A motor controller might be better to inherit from MotorController and CanObserver.

Obviously, you will likely have to rename almost all the class references in your .cpp and .h files.

# TASKING AND PRIORITIES

We hesitate to claim we have duplicated Linux and a real time operating system here. But the Arduino Due does sport an interesting set of clocks – 3 of them actually – each with 3 configurable interrupt timers for a total of 9 timer interrupts.

Inverter/controllers are operating powerful motors in real time and can be a bit demanding in that they want constant attention – regularly updated CAN control messages or they tend to shut down as a safety consideration. So inverters need the highest priority.

GEVCU does provide information to the user and allows configuration either by USB serial port or via a wireless web site. But while driving down the road, it would be quite normal for NO ONE to be using this at all to configure the system. So this is an example of a very low priority. Chargers and Battery Monitors and so forth would fall somewhere in between.

So we have developed a module called a TICK HANDLER. Your object module must register with this TICK HANDLER and then provide a public method, also termed TICKHANDLER to perform its duties as it can when the TICKHANDLER passes it a tick (timeslice).

You can think of your tickhandler as the LOOP routine in the Arduino Sketch/Processing environment or more traditionally MAIN.

To register your object with the tickhandler, the following general steps are in order.

1. Add a tickhandler DEFINE for your object to config.h file to set your tick interval in microseconds.

#define CFG_TICK_INTERVAL_EVIC 100000

Here, we define a tick interval for EVIC to call it every 100,000 microseconds (100 milliseconds)

2. Add a setup function to your object module establishing tickhandler

void EVIC::setup()

{

TickHandler::getInstance()->detach(this);//Turn off tickhandler

(Any number of other setup statements)

TickHandler::getInstance()->attach(this, , CFG_TICK_INTERVAL_EVIC);

}

In case our tickhandler is on, we turn it off. Perform any other setup functions desired. And then attach the tickhandler using the DEFINE from config.h.

3. Add a tickhandler function to your object module

void EVIC::handleTick()

{

sendCmdCurtis();

sendCmdOrion();

}

Here, we have a short function that calls two other functions. Each of those create and send a CAN command. So each 100 ms, the tickhandler will call the object function handleTick, which will send two CAN messages and return.

4. In your object module .h file, add the following includes:

#include "config.h"

#include "TickHandler.h"

# PERSISTENT CONFIGURATION STORAGE

Almost all modules in the GEVCU have some level of need to store information between operating sessions. This may be system data that you want to maintain from startup to startup such as accumulated Ampere-Hours or peak temperatures.

But almost all devices have some configuration options that end users can adjust to modify the operation of the software.

The Arduino Due ARM3 processor gives us very good power and speed for the VCU function, but it does not provide an EEPROM and the use of flash memory for persistent data has a problem in that it is totally erased if the software is updated.

So GEVCU has a 2Megabit (256kbytes) EEPROM provided just for such persistent data.

In coding independent objects that could be enabled in a variety of combinations, we have to have some means of rationalizing who stores what at what address and when. Otherwise, objects would be overwriting each other’s data.

Further, EEPROM’s have a defined write life. Not quite the issue it was originally, it is still nice to limit the number of writes so that the same data is not rewritten every 30 msec.

We do this with a device termed a MEMCACHE. An object has to register with DEVICES and is allocated a block of memory in MEMCACHE. The data in MEMCACHE is then recorded to EEPROM periodically. And it is loaded into MEMCACHE on startup. In this way, you can save your configuration data and load it again on the next startup.

1. Each device should create a configuration class that inherits from DeviceConfiguration. This will be in your .h file.

class EVICConfiguration: public DeviceConfiguration {

public:

};

2. The loadConfiguration() and saveConfiguration() methods of DmocMotorController and MotorController can be used as a reference for how to load and save configurations.
3. PrefHandler handles the memcache for various devices. Each device needs its own unique name and id number. These are held in the file DeviceTypes.h

enum DeviceId { //unique device ID for every piece of hardware possible

DMOC645 = 0x1000,

BRUSA_DMC5 = 0x1001,

CODAUQM = 0x1002,

BRUSACHARGE = 0x1010,

TCCHCHARGE = 0x1011,

LEAR=0x1012,

THROTTLE = 0x1030,

POTACCELPEDAL = 0x1031,

POTBRAKEPEDAL = 0x1032,

CANACCELPEDAL = 0x1033,

CANBRAKEPEDAL = 0x1034,

EVICTUS = 0x4400,

ICHIP2128 = 0x1040,

DCDC = 0x1050,

THINKBMS = 0x2000,

SYSTEM = 0x5000,

HEARTBEAT = 0x5001,

MEMCACHE = 0x5002,

PIDLISTENER = 0x6000,

ELM327EMU = 0x650,

INVALID = 0xFFFF

};

Here, for the EVIC class we call the device EVICTUS and assign the number 0x4400 to it.

In our object file EVIC.cpp, we have to alter our device constructor to include this.

EVIC::EVIC() : Device()

{

prefsHandler = new PrefHandler(EVICTUS);

commonName = "Andromeda Interfaces EVIC Display";

}

This registers us for the PrefsHandler to provide memcache space. We can then use LoadConfiguration and SaveConfiguration to handle our persistent data that we want to use from session to session without loss.

# MULTIPLE DEVICES ON CAN

GEVCU provides two independent CAN ports that can be configured for different speeds and operated more or less simultaneously. The nature of CAN is that a variety of hardware devices can be on the bus simultaneously as long as they all use the same data speed. And so of course a variety of object modules is envisioned, each servicing one or more CAN devices.

Again to accommodate this without chaos, we have developed a CAN handler. The CAN handler monitors the two CAN busses and when a CAN message is received, the message is passed to the appropriate module. And so each module performing CAN tasks must be registered with the CAN handler as to which specific CAN message IDs it wants to receive.

A canbus handler allows your device to register to receive frames that match the mask. The call to attach has four parameters. The first will basically always be “this”. The second is the ID to match, the third is the mask, and the fourth specifies whether you are interested in standard (false) or extended (true) frames.

canHandlerEv->attach(this, 0x230, 0x7f0, false);

canHandlerCar->attach(this, 0x650, 0x7f0, false);

In this case, we are registering with CAN bus 0 (Ev) to receive any message with an id between 0x230 and 0x23F.

We are also registering with CAN bus 1 (Car) to receive any CAN message with ID 0x650 through 0x65F.

If you need a quick refresher on masks and IDs: CAN bus filtering happens by taking every incoming frame and doing a bitwise AND with each registered mask in turn. The result of this is then compared to the associated ID for that mask. If the two match then your device will receive that frame. For instance, if a frame with 0x23D were to come in and the DmocMotorController had registered a mask of 0x7F0 and an ID of 0x230. 0x23D AND 0x7F0 = 0x230. This does match the ID and so DmocMotorController would get the frame.

Your class should have a handleCanFrame() method if you have registered one or more canbus handlers. This method takes a pointer to a CAN_FRAME structure as input.

# void DmocMotorController::handleCanFrame(CAN_FRAME *frame)

{

}

To send a frame, first create a CAN_FRAME structure variable, fill it out, and use sendFrame() to send it.

### CAN_FRAME output; //establishes variable output of structure CAN_FRAME

### output.length = 8; //Sets number of bytes in payload

### output.id = 0x207; //Sets message id

### output.extended = 0; //0 standard 11 bit frame 1 for extended 29bit frame

### output.data.bytes[0] = 0xa5; //This is simply puts value 5A

### output.data.bytes[1] = 0xa5; //in the first three payload bytes

### output.data.bytes[2] = 0x5a;

### output.data.bytes[3] = 0x00;

### output.data.bytes[4] = 0x00;

### output.data.bytes[5] = 0x00;

### output.data.bytes[6] = 0x00;

### output.data.bytes[7] = 0x00;

### CanHandler::getInstanceEV()->sendFrame(output); //Send the frame

IN this case we establish the variable output as type CAN_FRAME

We set the length to 8 bytes and the message ID to 0x207. We set it for standard 11bit frames and then populate the eight bytes with whatever we like. Then call the can handler to send frame OUTPUT. On the EV (CAN0) bus.

So note that we used a call to the can handler to register our ids and masks for incoming messages, and provided a method to handle those incoming messages by the specific name handleCanFrame.

We used another call to the canhandler to send a message we had preloaded into a CAN_FRAME variable.

In this way, all traffic is handled by the can handler and it can intelligently parse out CAN frames to hungry object modules waiting for them , and also stream messages onto the bus without collision or panic party.

The GEVCU project is designed such that the core system can be extended with modules that provide support for various pieces of hardware. Designing a new module is not conceptually complex but does require several things to be successful.

Note about formatting: BOLD words are class names. Italic words are file names. Underlined words are methods or members of a class. Methods are postfixed with ().

1. The first order of business is to find an existing module of hopefully the same basic type as your desired new module. For instance, if you hope to add support for an XYZ inverter then maybe you’d like to copy the DmocMotorController class. Rename the files with the same format. Maybe you’d name the files XYZMotorController.cpp and XYZMotorController.h If you cannot find an existing device of the same type then still use an existing set of files. The DmocMotorController class could be used as the basis for most any other device.
2. Rename all of the class references in the copied files as well.
3. Notice that DmocMotorController inherits from MotorController and CanObserver. If you are not creating a motor controller class then inherit from something else. Currently the other good choices are Throttle or Device. Device is always a decent choice if no more specific parent class exists. Inheriting from CanObserver is required if your device needs access to either of the CAN busses.
4. Each device can store data within EEPROM. Each device should create a configuration class that inherits from DeviceConfiguration. The loadConfiguration() and saveConfiguration() methods of DmocMotorController and MotorController can be used as a reference for how to load and save configurations.
5. Each device also must have a unique ID and should set what type of device it is. These are set with getId() and getType(). There is a global list of IDs that you should add your device to. DeviceTypes.h contains both the allowable device types and the ID of each and every device that is compiled into the firmware. You will note that DmocMotorController does not contain getType(). Instead it maintains the parent class version since it is still a motor controller.
6. Next, edit the constructor. Most of the constructor will be custom to your device but you will need to set prefsHandler to use your device ID constant instead of DMOC645. Also, set commonName to a nice, short description of your device.
7. Then there are several edits to make in the setup method. As shown in the DmocMotorController class, one should set up the tick handler, load the EEPROM configuration, call the parent setup (if applicable), and set up canbus handlers (if applicable).
  a. A tick handler allows your device to receive periodic ticks so that it can do processing at set intervals. This might be so that you can send canbus frames or so that you can check for input on one or more pins.
  b. Your class should have a handleTick() method if you have registered a tick handler.
  c. A canbus handler, handleCanFrame(), allows your device to register to receive frames that match the mask. The call to attach has four parameters. The first will basically always be “this”. The second is the ID to match, the third is the mask, and the fourth specifies whether you are interested in standard (false) or extended (true) frames. If you need a quick refresher on masks and IDs: Canbus filtering happens by taking every incoming frame and doing a bitwise AND with each registered mask in turn. The result of this is then compared to the associated ID for that mask. If the two match then your device will receive that frame. For instance, if a frame with 0x23D were to come in and the DmocMotorController had registered a mask of 0x7F0 and an ID of 0x230. 0x23D AND 0x7F0 = 0x230. This does match the ID and so DmocMotorController would get the frame.
  d. Your class should have a handleCanFrame() method if you have registered one or more canbus handlers. This method takes a pointer to a canbus frame as input.
8. As covered above, handleTick() and handleCanFrame() will form the majority of the action in most devices. Many devices will want to be able to send canbus frames out as well. This is done through CanHandler::getInstanceEV() or CanHandler::getInstanceCar(). The MotorController class pre-caches CanHandler::getInstanceEV() into the canHandlerEv member. To send a frame, first create a CAN_FRAME variable, fill it out, and use sendFrame() to send it. The DMOC sendCmd1 method shows how to do this.
9. If your device handler needs access to physical IO then use the systemIO member variable inherent to all devices. This variable references the SystemIO class which has the ability to interact with all of the digital I/O and analog inputs.
10. Now that the device handler has been constructed it is time to connect it with the rest of the system. In GEVCU.ino there is a function called createObjects(). You will need to instantiate your class here. You will also have you add your .h file as an include in GEVCU.h. With this done everything should automatically work. The system uses the PrefsHandler instance you setup in the class constructor to determine whether a given device is enabled and only sets up devices which are enabled.
11. A consequence of above is that you *must* enable your new device before it will do anything. This is done by typing “ENABLE=” followed by the ID of your new device.
1. Create your object.cpp and object.h files for your class. Often it is of help to copy an existing file set and rename them. If your new object is a motorcontroller, for example, use dmocMotorController.cpp and dmocMotorController.h. If it is a charger, copy a charger module.
2. List your device in DeviceTypes.h
3. Add your device as an include in GEVCU.h
4. Revise the createObjects section of GEVCU.ino to instantiate your class there.

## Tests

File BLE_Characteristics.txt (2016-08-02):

Outline of how to handle bluetooth:

Scan for BLE devices immediately when starting up. Get a list of them and then scan each one
 to see if it implements the 0x3100 service. If not then ignore it. Otherwise, pick
the first one to implement the service and start using it to get the characteristics.

Characteristics are:
0x3101 - TimeRunning (in seconds)
	4 bytes unsigned - number of seconds since GEVCU has started.

0x3102 - TrqReqAct
    2 bytes signed - Requested Torque in 0.1Nm increments
    2 bytes signed - Actual torque in 0.1Nm inc

0x3103 - ThrBrkLevels
    2 bytes unsigned - Raw Throttle value (from ADC)
    2 bytes unsigned - Raw brake value (from ADC)

0x3104 - Speed
    2 bytes unsigned - Requested RPM (always positive even for reverse)
    2 bytes unsigned - Actual RPM (always positive)

0x3105 - Modes (Writable)
    1 byte - Power Mode (0 = Torque, 1 = Direct RPM control)
    1 byte - Gear (0 = Neutral, 1 = Drive, 2 = Reverse, 3 = Error) - Writes to this are ignored.
    1 byte - IsRunning (True if we're currently drive enabled) - Writes are ignored
    1 Byte - IsFaulted (obviously, true if there is a fault) - Writes ignored
    1 Byte - IsWarning (True is there is currently a warning in effect) - Writes Ignored
    1 Byte - LogLevel (0 = Debugging, 1 = Info, 2 = Warn 3 = Error 4 = Off)

0x3106 - PowerStatus
    2 bytes unsigned - Bus Voltage in tenths of a volt
    2 bytes signed - Bus Current in tenths of an amp
    2 bytes signed - Motor Current in tenths of an amp
    2 bytes unsigned - Kilowatt hours left in the battery pack (in full kwh)
    2 bytes signed - Mechanical power in 0.1 kw increments

0x3107 - Bitfields
    4 Bytes unsigned - Bitfield 1 - All these bitfields are set by the motor controller code
    4 Bytes unsigned - bitfield 2 - There doesn't seem to be any standardization here. 
    4 Bytes unsigned - bitfield 3 - And, only the Brusa controller code even touches these.
    4 Bytes unsigned - bitfield 4

0x3108 - Temperature
    2 bytes signed - Motor temperature in 0.1C increment
    2 bytes signed - Inverter temperature in 0.1C increment
    2 bytes signed - System temperature in 0.1C increment

0x3109 - DigitalIO (Writable)
    2 bytes unsigned - Precharge resistance in ohms (used to figure out how long the timing should be)
    1 byte - Which digital output to use for precharge
    1 byte - Which digital output to use for the main contactor
    1 byte - which digital output to use to actuate cooling fans
    1 byte - Temperature in C at which to turn on the cooling fans
    1 byte - Temperature in C at which to turn them off again
    1 byte - Which digital output to use for brake lights
    1 byte - Which digital output to use for reverse lights
    1 byte - Which digital input to use for enabling motor controller drive
    1 byte - which digital input to use for going into reverse (instead of drive)

0x310A - ThrottleIO (Writable)
    1 Byte - Number of throttle inputs (only really relevant to POT based throttles). 1-3 inputs on ADC ports
    1 Byte - Throttle type (1 = Standard Pot, 2 = Inverse Pot)
    2 Bytes Unsigned - Throttle 1 Minimum Value
    2 Bytes Unsigned - Throttle 2 Minimum Value
    2 Bytes Unsigned - Throttle 1 Maximum Value
    2 Bytes Unsigned - Throttle 2 Maximum Value

0x310B - ThrottleMap (Writable)
    2 Bytes unsigned - Pedal position (1/10 of a %) where regen is at its maximum
    2 bytes unsigned - Pedal position where regen is at its minimum
    2 bytes unsigned - Pedal position where forward motion starts
    2 bytes unsigned - Pedal position where 50% power is applied
    1 byte - Percentage of full torque to use for minimum regen
    1 byte - Percentage of full torque to use for maximum regen
    1 byte - percentage of full torque to use for creep

0x310C - BrakeParam (Writable)
    2 bytes unsigned - ADC value for minimum brake signal
    2 bytes unsigned - ADC value for maximum brake signal
    1 byte - Percentage of full torque to use for minimum brake regen
    1 byte - Percentage of full torque to use for maximum brake regen

0x310D - MaxParams (Writable)
    2 bytes unsigned - Nominal battery pack voltage (1/10 of a volt)
    2 bytes unsigned - Maximum RPM to allow
    2 bytes unsigned - Maximum torque to allow

0x31D0 - Update counter (just for debugging)
    4 bytes unsigned - counter that increments as other updates happen. Probably shouldn't subscribe to this as a notification. But, useful for debugging

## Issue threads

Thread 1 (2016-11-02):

Further work on BLE code in DEV branch

collin80, 2016-11-02:
At the moment the DEV branch has a very large rewrite of the BLE driver. It mostly works but sometimes commands to the BLE module fail and also it seems to not be reliably updating GATT characteristics quite as frequently as it should. Testing has revealed that it actually seems to get better as the update frequency is lowered. Investigate the source of the remaining issues.

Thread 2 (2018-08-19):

Problems with 6.35

bsculley, 2018-08-19:
The current version of the software (downloaded from the EVTV website) is 6.35.  It does not compile due to apparent naming issues with Adafruit library. (BLE.h vs. Adafruit_BLE.h).

I installed the current Adafruit library and changed the names of the .h files to include the Adafruit_ prefix, but then got some very ugly errors regarding missing methods, unknown types, etc.

There seems to be nothing here that matches version 6.35.
Can you provide any guidance on what version to use and where to get it?

collin80, 2018-08-20:
When in doubt, get the version from my github repos, not any versions from elsewhere. Last I knew the bluetooth library I have does work with GEVCU. You will probably need to update all libraries including due_can and can_common.

bsculley, 2018-08-20:
Hi, thanks for the response.

I downloaded your GEVCU6 repo.  It compiles and seems to support the current hardware, maybe...  GEVCU user guide says 6.22, but the comments in the code specify 6.23c.  It would be nice to know what the offset represents, if you know.

I will also get current copies of the due_can and can_common libraries as you suggest.

Anything else you can think of that might be helpful will be greatly appreciated.

Thanks again,

Bob

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

collin80, 2018-08-21:
The BLE library needs to be the "development" branch from my repo, not master branch. I just found this out. Apparently I forgot about this from 2 years ago when it was done. This the link for the proper version: https://github.com/collin80/Adafruit_BLE_SPI/tree/development

Sorry for the inconvenience.

bsculley, 2018-08-21:
Hi Collin,

I downloaded the correct libraries (including current versions on can_due and can_common) as well as FirmwareReceiver.

I am now left with only one error:  'EMAFilter' does not name a type

Hopefully you can shed some light on this.

Thanks,

Bob

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

collin80, 2018-08-21:
Pardon, it's been about 2 years since I had last set up to compile the code and had forgotten a few libraries. You need this one too:
https://github.com/collin80/Microsmooth

I will add this to the readme.

bsculley, 2018-08-22:
All good now.

Thanks for the timely support.

Bob

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

bsculley, 2018-08-28:
Hi Collin,

One last? question.  Does the software support J1939 (29 bit ID) messages?

I plugging through the low level code but haven’t found anything yet.

Thanks,

Bob

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

collin80, 2018-08-28:
It should but that has not been well tested. Everything we've been using has been standard IDs.

bsculley, 2018-09-03:
Hi Collin,

Thanks for your previous help.

I now have the GEVCU working to some extent, but am having the following problem:

If I upload the pre-compiled binary from the EVTV site, everything works as advertised.

If I compile the code, it uploads and appears to run ok (heartbeat LED is flashing), but the serial port doesn’t work.

I have tried uploading from the IDE and also tried creating a binary file and using the binary uploader, all with the same result:

The file uploads fine, but when I reset the GEVCU I get a composite USB device in the device manager with status 10 (Device cannot start) and no serial port.

I have tried both the 6.35 source from the EVTV site and the source from your GEVCU6 GitHub repo.

Hopefully I’m doing something stupid, in which case sorry to bother you, but I would appreciate any thoughts you have on this.

Thanks,

Bob

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

bsculley, 2018-09-04:
Further to this issue, it seems that _any_ sketch developed from source has the same symptoms, so it seems to be some issue between the Arduino IDE and the GEVCU board.  I am using v1.8.5 of Arduino.  Any idea what could be causing this?

collin80, 2018-09-04:
Well, it's good news that the precompiled binary from EVTV works with the hardware. That seems to prove that the hardware itself is fine. But, not so good news that compiling it yourself breaks every time. I must confess, there's a reason the files in this project are about 3 years old. They haven't been touched in that time. It's possibly a library issue. Though now I'm seeing you posted that any sketch breaks but the previously pre-compiled binary works. Hmmm... Have you tried very simple sketches just to prove that your Arduino installation isn't broken? Maybe just:

```
void setup()
{
}

void loop()
{
    SerialUSB.println("This is working");
    delay(1000);
}
```

bsculley, 2018-09-04:
Hi Collin,

Yes, I have tried dirt simple sketches, but with the same results.

Other microprocessors. Teensy, etc. work fine, so I think the basic environment is Ok.

Somehow, the USB device ID is changing, from USB\VID_2341&PID_003E&MI_00\6&7B4334&1&0000, which works, to  USB\VID_2341&PID_003E\5&2c705bfe&0&1 which doesn’t work.

This is driving me crazy!

Bob

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

collin80, 2018-09-04:
Yes, that sounds pretty irritating. I'm sorry you're having such trouble. Unfortunately each microprocessor has its own core and sometimes even a different compiler. So, it can be hard to prove that it is working properly by compiling for other systems. If you had an Arduino Due of some sort to test against that would help - maybe an EVTVDue or a plain Due or something like that. Then we could rule out the device itself as being the culprit though the fact that the binary updater works would tend to suggest that the hardware is functional. That simple sketches don't even work points toward it not being an issue with GEVCU code or the other hardware support libraries for things like CAN. All of this circles back around to there being some sort of brokenness with the Arduino installation. It wouldn't be the first time I've heard of that happening. Lame as this is going to feel, you might need to see if you can borrow time on another machine and clean install Arduino with the Due files and then try out something as simple as the sketch I posted to make 100% sure it isn't your computer or the Arduino installation on that computer. It can be pretty irritating. Arduino is supposed to make it easier for novices to get started with development but sometimes it makes it easier for obscure errors to manifest behind the scenes with no clearly defined cause. Hopefully all of this helps.

collin80, 2018-09-04:
Somewhat annoyingly, they changed the way libraries work, I think for the 1.6 and newer IDE releases. So, the likely possibility is that the libraries go somewhere else for that version. No, I don't remember specifics. But, so long as you've got it installed, try out 1.5.4 with a simple program and see if the GEVCU still locks up. You might be able to fix things as simply as deleting everything related to the Arduino IDE and starting over. Yeah, perhaps that doesn't sound very simple but sometimes it does have to happen. I'm pretty sure it has happened to Jack before and it happened to me once a couple of years back. Sometimes you have to nuke it from orbit to be sure then rebuild it.

bsculley, 2018-09-04:
I think I have solved this by re-installing the latest version of the Due board.

Hopefully I have not worn out my welcome here, as I’m sure I will still have some hurdles to overcome.

Thanks,

Bob

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

collin80, 2018-09-04:
Don't worry about it, I know the Arduino IDE is like that. Sometimes it gets into a weird state and for reasons no one can explain it just plain ruins everything it touches until you delete everything and start over. Sometimes you can use the board manager to remove the files then install the new version, sometimes you have to nuke the whole IDE and find where it stores its files and zap those too. Hopefully you've shown it who's boss now and things will work better.

bsculley, 2018-09-05:
Thanks.

Yaweh1957, 2020-09-06:
Hi Collin,
Really require your expertise! I am new to this game but willing to learn! My headache is such, a week ago I could communicate with the GEVCU through Arduino but had major hiccup communicating with the DMOC through CCShell. The role has now reversed and I have comm's with the DMOC, but for some unknown reason, I simply cannot connect with the GEVCU. The Arduino software correctly loads/recognizes the board type ( Arduino Due native usb) and port. Running version 1.8.12. Opening the serial monitor shows no heartbeat. I have two of these boards, both giving the same result. I did try out a test sketch,( File, Examples, Basic, Blink,upload) The return message said, that the thread was successful and the CPU had been reset? Did I inadvertently Nuke he programme??? If so, how do I go about downloading the software, what version and where would I locate such? Really in a sticky spot! Will appreciate any advice/guidance from anyone on the forum. Kind Regards from SA! Fred.
fred@yawehelectrical.co.za

collin80, 2020-09-06:
When you flashed the test sketch, did it do anything? GEVCU has it's only software switchable LED on digital pin 13  just like the blink sketch is expecting. As such, you should see the LED blink when you run that sketch. If it does then you can successfully compile and upload sketches which is good to know. Now, this DOES erase the normal GEVCU program. So, you'd then have to re-upload GEVCU6 to get back up and running. EVTV has a link to a binary updater that can be used to replace the firmware on the board without having to get everything set up to compile it yourself: http://media3.ev-tv.me/GEVCUupdate6.zip

larsrengersen, 2020-09-07:
Last week I had issues with 1.8.12 while working on CAN-BUS. Small sketches loaded fine, but bigger ones were not successfully uploaded and only partially worked. Very strange. Upgraded to IDE 1.8.13 and it now works fine again. Hope that works for you too.

Closed 2018-09-05.

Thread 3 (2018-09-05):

Multiple Motor support

bsculley, 2018-09-05:
I am confronted with a project in which the vehicle has two separate motors, separately controlled (one per each rear wheel).

Everything is separate, drive mode, temperatures, cooling, power, CAN id's...  The power mode, demands, etc. are intended to always be synchronized, but the motors have to turn in opposite directions.  Before you say anything, I didn't design it, I'm only the software guy.

I started out thinking I could just use two instances of MotorController, but it became clear that there are a lot of places that assume there is only a single MotorController. I don't know if you have any interest in this problem, if not fine, I certainly can understand.  But if you have ever thought about it, I would appreciate any ideas you may have come up with.  I'd like to stay "in the spirit" of the architecture.

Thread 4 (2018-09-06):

CAN Bus not working

bsculley, 2018-09-06:
I am having problems getting the GEVCU CAN bus to work.  I am using CAN0, with A2 as CANH0 and B2 as CANL0 on the 30 pin connector.  I have the PowerKey keyboard and a CAN monitoring board on the CAN network (both at 500000 baud).  I can see the CAN messages from the PowerKey, so I think the bus is functioning ok.

I put a log trace in at CanHandler::process, with the following results:

9246 - INFO: CAN: status=2162880 speed=500000
9247 - INFO: CAN: status=1151729664 speed=500000
9248 - INFO: CAN: status=2162880 speed=500000
9250 - INFO: CAN: status=1151729664 speed=500000

I have no way to interpret the status values.

I have tried simple hardware debugging:

Resistance (unpowered) between CANH0->GND and CANL0->GND seems to be infinite (no reading) in both cases.

The voltage (powered, obviously)  between CANH0->GND and CANL0->GND is 0 in both cases.  All measurements are at the wires from the 30 pin connector.  I have verified that the multi-meter is working.  Other devices show nominal readings.

Don't know what I'm doing wrong.  Any ideas gratefully accepted.

bsculley, 2018-09-07:
Further to this issue, I have tried using CAN1 with the same results.

collin80, 2018-09-07:
With the CANH0 and CANL0 wires not connected to anything else what is the resistance between them? It should be 120 ohms. They're isolated floating differential wires you won't necessarily get good readings to ground. You can basically only read between them. It's been too long since I saw where those status flags even come from. I'll try to look that up.

bsculley, 2018-09-08:
Thanks for the tip.  I get 120 ohms between the H/L lines when measured at the terminals on the GEVCU, however, I get nothing when measured at the ends of the wires on the cinch plug.  I have verified that it is seated as far as possible and, in fact, some other terminals are connected, e.g. A0.

I have gotten the CAN working by connecting some jumper wires directly to the terminals on the GEVCO.  I believe there is some defect in the cinch plug wiring or mechanics.

Bob

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

Closed 2018-09-08.

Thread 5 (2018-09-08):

CAN transmission of extended messages is not working

bsculley, 2018-09-08:
I have gotten CAN messaging working now.  I am able to communicate between GEVCU and the PowerKey Pro.  I am monitoring the CAN traffic with a teensy using a SN65HVD230D tranceiver and the FlexCAN_Library.  I can see the button presses from the PowerKey and the GEVCU response to set the LEDS.

What is not working is sending extended frames.  Here is the routine that sends the frame:

```
bool FaradayMotorController::getBaseValues(int motor) {

  CAN_FRAME requestFrame;
  bool result;

  uint8_t buf[] = {0x0A, 0xFF, 0x00, 0x00, 0x00, 0x00, 0x00, 0x00};
  requestFrame.extended = 1; //J1939 frame
  requestFrame.fid = 0; //?
  requestFrame.priority = 7;
  requestFrame.rtr = 0;
  requestFrame.length = 3;
  uint32_t i = 0xEA00 + motor;
  requestFrame.id = (i << 8) + 0xF9;
  memcpy(requestFrame.data.bytes, buf, 8);

  result = canHandlerEv.sendFrame(requestFrame);

  Logger::info("info request sent: %X result %d ", motor, result);
  return true;
}
```
Here is the CanHandler sendFrame routine:

```
bool CanHandler::sendFrame(CAN_FRAME& frame)
{
  logFrame(frame);
  return bus->sendFrame(frame);
}
```

Here is the serial output on GEVCU:

```
32867 - INFO: CAN: ext=0x1 rtr=0x0 pri=0x7 fid=0x0 id=0xEA00F9 len=3 data=0xA,0xFF,0x0,0x0,0x0,0x0,0x0,0x0
32871 - INFO: info request sent: 0x0 result 1
```
Everything appears to be working.  No errors and a good return from bus->sendFrame, but nothing shows up on the wire.
When I change the extended setting to 0 (no other changes), then I can see the frame, although somewhat mangled. Output from the serial port on the teensy:

`CAN 0:  ext=0 rtr=0 pri=0 id=F9 len=3 0a ff 00
`
It appears that there are issues with the extended frames.  What is the "family id" is this something I should be using with extended frames?

I Considered replacing the due_can library with FlexCAN, but I'm not sure how big a "can" of worms that would be.

As always, any help will be greatly appreciated.

Bob

bsculley, 2018-09-11:
Sorry.  Turned out I wasn't receiving the extended frames.

Closed 2018-09-11.

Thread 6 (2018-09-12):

Failure to receive extended frames

bsculley, 2018-09-12:
Hi Collin,

I posted a parallel issue on the due_can repo.  I am not able to get the GEVCU to receive extended frames.  I tried the CAN_ExtendedPingPong example from the due_can library and was seeing the same result.

I have done this in GEVCO.35.ino setup:

```
	for (int filter = 4; filter < 7; filter++) {
		Can0.setRXFilter(filter, 0, 0, true);
	}
```
and this in the setup of my custom motor controller:

`	canHandlerEv.attach(this, 0xF9, 0x1FFFFFFF, true);
`

Hopefully I'm just doing something wrong, but I sure can't see it.  I could use a boost here.

bsculley, 2018-09-12:
Further to this issue, I have also tried using watchFor() in place of setting up explicit filters, but it had no effect.

collin80, 2018-09-12:
I'm going to try to look into it further. The odd part is that I just
recently used a different board but with the same processor and CAN library
and it was receiving extended frames perfectly well.

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

bsculley, 2018-09-12:
Never mind.  I was using the filter mask all wrong.  Sorry.

Closed 2018-09-12.

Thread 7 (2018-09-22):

Adafruit implementation

bsculley, 2018-09-22:
Hi Collin,

I am trying to implement the Adafruit module on GEVCU 6.2.   I have the module connected and configured in GEVCU, but I'm not able to see a Bluetooth device.

`5147 - INFO:  - add device: AdaFruit BLE (id: 0x1041, 0x20074EE0)`

Do I need to do anything besides connecting it and enabling the device?

Thanks,
Bob

collin80, 2018-09-25:
Umm... Sadly, I don't remember. It's probably been 3 years since I tried to
use an Adafruit BLE module with a GEVCU6.2. Hmm. What does it say when you
enable debugging output? (LOGLEVEL=0 on the console). That might help to
narrow it down.

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

bsculley, 2018-09-26:
Here's the log starting from an 'a' reset.  At the end, the DATATYPE=2 error repeats forever:

```
ADABLUE reset
209847 - DEBUG: New checksum: BF
210723 - DEBUG: Set new BLE state: 1
210725 - DEBUG: Factory Resetting BLE
211124 - DEBUG: New checksum: BF
211843 - DEBUG: Set new BLE state: 2
211845 - DEBUG: Sending power level cmd
211854 - DEBUG: Cmd completed as true in state 2
211856 - DEBUG: Set new BLE state: 3
211883 - DEBUG: Sending device name cmd
211957 - DEBUG: Cmd completed as true in state 3
211958 - DEBUG: Set new BLE state: 4
211963 - DEBUG: Sending add service cmd
211972 - DEBUG: Got a new line: 1
211973 - DEBUG: Cmd completed as true in state 4
211975 - DEBUG: Set new BLE state: 5
212003 - DEBUG: Sending characteristic definition
212404 - DEBUG: New checksum: BF
213203 - DEBUG: Sending characteristic definition
213224 - DEBUG: Got a new line: Option Error: UON=TimeRunning
213225 - DEBUG: Cmd completed as false in state 5
213227 - DEBUG: Error setting characteristics!
213243 - DEBUG: Sending characteristic definition
213264 - DEBUG: Got a new line: Option Error: DATATYPE=2
213265 - DEBUG: Cmd completed as false in state 5
213267 - DEBUG: Error setting characteristics!
213283 - DEBUG: Sending characteristic definition
213304 - DEBUG: Got a new line: Option Error: DATATYPE=2
213305 - DEBUG: Cmd completed as false in state 5
213307 - DEBUG: Error setting characteristics!
213323 - DEBUG: Sending characteristic definition
213345 - DEBUG: Got a new line: Option Error: DATATYPE=2
```

collin80, 2018-09-27:
Hmmm.. It seems to work for a little bit then fail and get stuck. And, it seems to be corrupting the lines a little bit. For instance, it should be PRESENTATION= not URESTENTATION=, things like that. It seems like U's are getting inserted in there randomly. Maybe the SPI link is going too quickly? It's also possible that they updated the API in the meantime. The code in GEVCU was written in 2016 apparently and recently Adafruit has been updating the firmware again. Have you updated the firmware on your BLE module recently? I'll try to dig up an Adafruit BLE module on my end and see if I can get it to work.

bsculley, 2018-09-27:
Further to this issue, I have managed to connect to the BLE device using the Adafruit android app.  I see the device being advertised as GEVCU 6.2 ECU, but the firmware update failed with error DFU DEVICE DISCONNECTED.  Is there something I need to do on GEVCU for this to work?

collin80, 2018-09-27:
When I asked about the firmware version I was referring to the Adafruit
module itself, just to be clear. It sounds like you tried to do that with
their Adafruit app which is the proper way to do it. It ought to work. I've
updated BLE firmware through their app before. If it won't do it then
perhaps you've got a questionable module that just doesn't quite work
properly.

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

bsculley, 2018-09-27:
I have asked about it on the Adafruit forum.  Maybe I'll get an answer.
Can you confirm a version of the firmware that works with GEVCU?  The module I have is 0.6.5.

bsculley, 2018-10-04:
I bought a new Bluetooth module and am getting the same results as before.  Device software is revision 0.6.5.  Should I upgrade it?  I really need to get this working.

```
36879 - DEBUG: Cmd completed as true in state 4
36880 - DEBUG: Set new BLE state: 5
36884 - DEBUG: Sending characteristic definition: TimeRunning
36906 - DEBUG: Got a new line: Option Error: DATATYPE=2
36907 - DEBUG: Cmd completed as false in state 5
36909 - DEBUG: Error setting characteristics!
36924 - DEBUG: Sending characteristic definition: TimeRunning
37045 - DEBUG: New checksum: BF
38084 - DEBUG: Sending characteristic definition: TimeRunning
38106 - DEBUG: Got a new line: Option Error: UON=TimeRunning
38107 - DEBUG: Cmd completed as false in state 5
38109 - DEBUG: Error setting characteristics!
38124 - DEBUG: Sending characteristic definition: TimeRunning
38145 - DEBUG: Got a new line: Option Error: DATATYPE=2
38147 - DEBUG: Cmd completed as false in state 5
38149 - DEBUG: Error setting characteristics!
```

collin80, 2018-10-05:
So, where does that leave you? Well, actually the first unit I tried did nothing because it was a UART version of the board. You see, there were many versions of the GEVCU6 design before we settled upon the latest one. First we used very cheap BLE modules that were not configurable - they just were BLE to UART chips. Then we switched to Adafruit but the UART version. Then we switched to the SPI version to try to get more speed. I believe you must have the newest, SPI version or you wouldn't get anything at all. With the UART version youd be stuck at state 2 forever trying to set the power level. Anyway, so you probably have the newest board version but something is still not working. First of all, use the DEV branch of GEVCU6 because it is newer and has updates compared to the master branch. That's the version I'm testing with. Then, just to be sure, use the Adafruit library I've put here: www.savvycan.com/Adafruit_BLE_SPI.zip

Between those two things it ought to work because I did just test and was able to get to a stable state and see it with the Adafruit android app.

collin80, 2018-10-05:
Lastly, if you've already modified things elsewhere in the code and don't want to overwrite all your changes, then try grabbing just adafruitBLE.cpp and adafruitBLE.h from the DEV branch. Those two files should be the only ones you really need to fix BLE but there were a LOT of BLE related commits between MASTER and DEV so I can't say for 100% sure nothing changed outside those files but it shouldn't have. It is intentionally object oriented and segmented.

bsculley, 2018-10-05:
I downloaded and installed the Adafruit library.  Nothing much changed, just a new error.  I'll try the DEV version of GEVCU tomorrow.  Are most of the changes to the AdafruitBLE files, or are they more widespread?
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
bsculley, 2018-10-24:
I bought yet another Bluetooth module, and this one seems to work.  I still can't start it in verbose mode, but I was able to update it to 0.8.0 and the characteristic definitions and updates seem to be working.  I am trying to use the ELM327 interface with the Torque android app, but it's not working.  I have paired the Bluetooth module with the tablet but Torque won't connect to it.  Is there something I need to do to get this to work?  What software have you used successfully with the ELM327 emulation?

collin80, 2018-10-24:
Well, it's strange that you could have gotten 2 bad modules in a row. But, good that you got it mostly working. Now, the ELM327 emulation I think was done with a previous bluetooth module. You can't really do ELM327 over BLE. The ELM327 emulator code thus sends to a serial port that the older bluetooth module listened to. In theory Torque could access ELM327 devices over WiFi which still doesn't quite work out for you with a standard GEVCU6. I believe we left in code to respond to OBDII queries on CAN so you could add an ELM327 compatible dongle to your CAN bus.

bsculley, 2018-10-24:
Thanks for the reply, but I'm a bit at sea here.  We assumed that since there was an ELM327 emulator that we could use the Bluetooth module to access it.  The Torque app has been upgraded to work with BLE (at least according to their docs).  Are you saying that that the ELM emulator won't work with the Adafruit Bluetooth module?  If not, then what will work with it?  Is there any Bluetooth client software that will work with GEVCU in its current configuration?  Is there additional development that would make this work?

We need a way to implement a dashboard and collect operational data from the vehicle using Torque or something like it.  What options do we have for this using GEVCU, including the client software?  If we need an ELM compatible CAN/Bluetooth module, can you recommend one?

Sorry if I'm being stupid, but this is a surprise and not a good one.

collin80, 2018-10-25:
Hmm, I didn't know Torque was starting to support BLE. Perhaps that would be an approach. I'll have to look into it. The ELM327 stuff is brought over from previous revisions of the board where we did use a standard bluetooth module. But, if BLE will work then I can probably get the Adafruit module to work with Torque. Otherwise an OBDII connected bluetooth adapter could connect to torque and turn the Torque requests into CAN messages which the GEVCU6 board could then respond to.

bsculley, 2018-10-26:
Ok, thanks.  Ideally we would like Torque to work with the BLE adapter, which it says it will do (v1.8.199).
https://torque-bhp.com/forums/?wpforumaction=viewtopic&t=3.0
Let me know if there is anything I can do to support your effort.

bsculley, 2018-11-01:
Have you had a chance to look into this?

collin80, 2018-11-05:
I have looked into it and it seems possible but I haven't had time to get
it all set up yet.

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

bsculley, 2018-11-06:
Great news.  Please keep me apprised.

bsculley, 2018-11-09:
I appreciate your attention to this.  For planning purposes, it would be helpful to know in what timeframe you think this might be resolved.

Thanks.

bsculley, 2018-11-20:
I'm hoping that no news is good news?

collin80, 2018-11-22:
Well, it isn't bad news per se. I did look into it more and it really does seem pretty straight forward. But, I just haven't had any time to actually attempt it. Perhaps this weekend I might get some testing done.

bsculley, 2018-11-22:
Excellent, thank you.

bsculley, 2018-12-04:
Any update?

bsculley, 2018-12-10:
Hi Collin,

Our project is a bit on hold pending a resolution of this.

Can you provide any kind of an estimate as to when this feature might be available for testing?

Thanks,

Bob

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

collin80, 2018-12-10:
Yeah, I'm sorry it's taking so long. Lots and lots of projects are in the works right now. I actually did all the coding I think it should take to make it work but I haven't tested it yet. So, hopefully it works the first try and everything is good. Though, is that likely? Probably not. I will try to remember to grab a GEVCU6 with BLE module and test. I don't actually have as many of them as you might think so I've got to go searching to find a good one and not some pre-release broken hardware.

bsculley, 2018-12-24:
Hi Collin,

Just checking in to see if there is any progress.

If you’re far enough along I would be happy to help with the testing.

Merry Christmas.

Bob

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

bsculley, 2019-01-10:
Hi Collin,

I hope the new year finds you well.  In your last communication you said you had completed the coding and testing is pending.  Great news!  If I can be of any help in testing please let me know.  Looking forward to hearing the current status.

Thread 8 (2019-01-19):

Serial Port problem in 6.35

DimitriosGk, 2019-01-19:
Hello,

We seem to have an issue with the serial monitor of the last release of your sw. The software gets uploaded succesfully (checked it by using the BLINK_LED also), but when i open the serial monitor nothing seems to be going on. At the same time, the PORT loses connection repeatedly, tested in more than 2 computers.

I tried unistalling everything and installing again but the problem persists (Including due libs & drivers etc.). I used the old sw (for versions until GEVCU 4) and it works fine with the serial, but in this one it does not recognize the inputs (I connected a potensiometer and checked that it works with a multimeter also-the input never showed up on the serial monitor), probably because of some changes in the pinout of the newer versions of GEVCU.

Do you have any solution in mind for that problem?

Thank you,

collin80, 2019-01-19:
I assume you're compiling it yourself? If so, try the binary updater from
EVTV: http://media3.ev-tv.me/GEVCUupdate6.zip and see if that works. Also,
you might try the "DEV" branch of GEVCU6. I have been using that branch in
a car so I know it works. I'm don't think I've used the master branch
recently. I thought it was stable but perhaps there's an issue with newer
libraries or Arduino version.

On Sat, Jan 19, 2019 at 6:33 AM Dimitrios Gkotsoulias <
notifications@github.com> wrote:

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

DimitriosGk, 2019-01-20:
Hi,

Thanks for the answer.
I tried the .bin files but no luck either. Even if the .bin of a previous compile works, we need the source code to d changes etc. Where can i find the DEV branch of GEVCU6? I dont seem to find it in the GEVCU6 git repository.
One more note: I have tried to print using serialusb.println() in the serial monitor and it works properly. Then I try to add modules within my .ino (adding the relevant cpp and .h files) and until some point i can see the message on the serial monitor as well as the led blinking, as i have commanded (for check) in the loop(){}. After adding wire.begin... and memchace instructions it fails to get in the loop and just projects repeated warnings and info messages to the console regarding the values of the config file. It never prints the menu nor the heartbeat either.
What is the last stable arduino version you compiled and worked with?
Should I work with the updated libraries or  with the ones that i can find in your git repository?

DimitriosGk, 2019-01-20:
Hi,

Thanks for the answer.
I tried the .bin files but no luck either. Even if the .bin of a previous compile works, we need the source code to d changes etc. I will try the DEV branch.
One more note: I have tried to print using serialusb.println() in the serial monitor and it works properly. Then I try to add modules within my .ino (adding the relevant cpp and .h files) and until some point i can see the message on the serial monitor as well as the led blinking, as i have commanded (for check) in the loop(){}. After adding wire.begin... and memchace instructions it fails to get in the loop and just projects repeated warnings and info messages to the console regarding the values of the config file. It never prints the menu nor the heartbeat either.
What is the last stable arduino version you compiled and worked with?
Should I work with the updated libraries or with the ones that i can find in your git repository?

collin80, 2019-01-21:
Sorry I apparently wasn't clear what I was asking. I hoped you might
show me what the serial console says when it boots up. In there should
be a lot of debugging messages that will help to figure out why it
doesn't work.

On Sun, Jan 20, 2019 at 2:24 PM Dimitrios Gkotsoulias
<notifications@github.com> wrote:
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

DimitriosGk, 2019-01-21:
Same if i do almost the same changes on the DEV branch. I get repeatedly:
44854 - WARNING: DMC5 - Invalid checksum, using hard coded config values
44858 - DEBUG: New checksum: 5D
44873 - INFO: Checksum matches Value: 0x5D
44875 - INFO: Valid checksum, using stored config values
44877 - INFO: MaxTorque: 32 MaxRPM: 1873
44878 - WARNING: DMC5 - Invalid checksum, using hard coded config values
44883 - DEBUG: New checksum: 95
44897 - INFO: Checksum matches Value: 0x95
44899 - INFO: Valid checksum, using stored config values
44901 - INFO: MaxTorque: 8199 MaxRPM: 59820

So the problem is that it never reaches to the point of loop(). Something is going wrong in setup, after lines digitalWrite(BLINK_LED, LOW);. I set the led HIGH to see if i get there and it actually reaches up to that point. Then it looks like it is reseting, the led goes LOW and we hear the sound of unpluging the board. This happens continouusly with somethong like 10 seconds between its time. The LED goes HIGH and then again LOW with unpluging sound.
Is there any reason that the device would be reseting?

collin80, 2019-01-22:
Weird... I suppose it might have something to do with the DMC5 code. You
see, I've never once enabled that device personally. Someone else wrote it
and used it and it was for the GEVCU4 code. To my knowledge no one has
tested it in GEVCU6. It's possible that some changes broke the code and
since no one needed that device to work it sat broken since. I'll have to
give it a try and see if using that device breaks for me too. Currently
there isn't any good way to quit using a device if it breaks things before
you can get to the serial console. You can, of course, comment out that
device so it doesn't get added to the system but that doesn't do you a lot
of good.

I do have to wonder, did it mess up before you enabled the DMC5 device? I
really do wonder if the whole problem is in that code.

On Mon, Jan 21, 2019 at 8:40 AM Dimitrios Gkotsoulias <
notifications@github.com> wrote:

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

collin80, 2019-01-22:
It seems that indeed the code to support the DMC5 was broken at some point
and it was never used so no one ever noticed. If you comment out line 354
which is saveConfiguration(); and found directly
under config->enableOscillationLimiter = false; then it should work. It
looks like someone started to support loading settings from EEPROM but
never got 100% of the way there and then it was left as a mess. For now
just comment out the call and maybe even everything within the
saveConfiguation function just to be safe. I'll try to fix it all up soon
so that it actually supports saving the settings to EEPROM like it should.
In the meantime everything will be hard coded as far as settings go.

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

chadman98126, 2020-02-10:
perhaps it's worthwhile to check these changes into the Dev and/or Main branches?  (to avoid this issue until the save to EEPROM call(s) are fixed)

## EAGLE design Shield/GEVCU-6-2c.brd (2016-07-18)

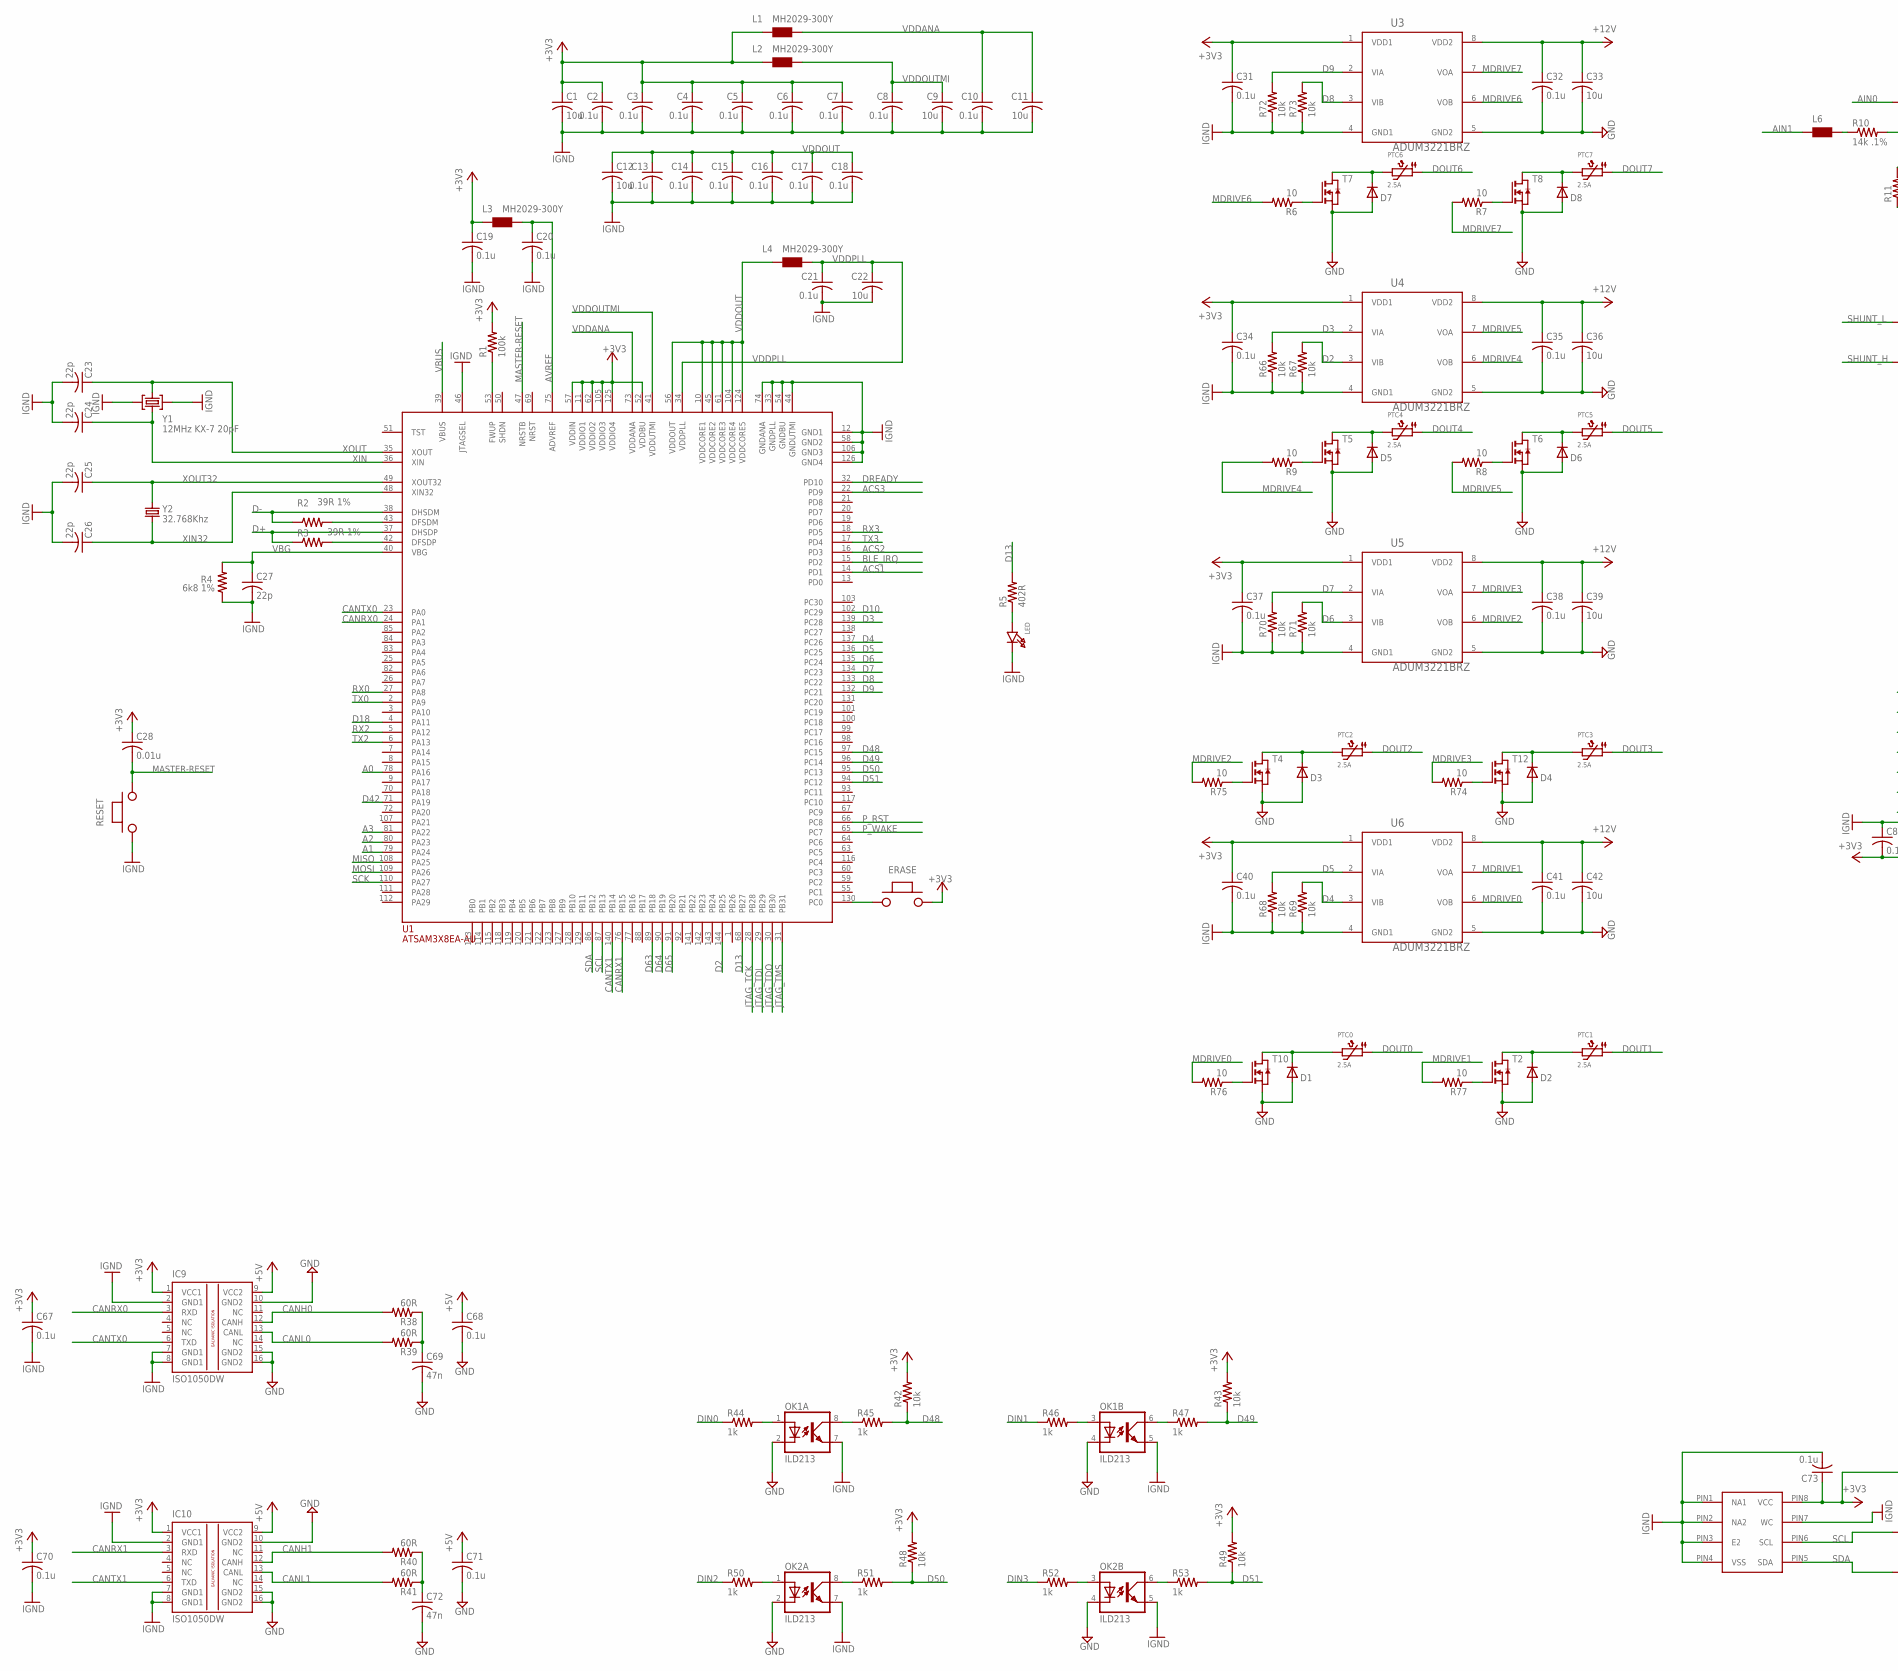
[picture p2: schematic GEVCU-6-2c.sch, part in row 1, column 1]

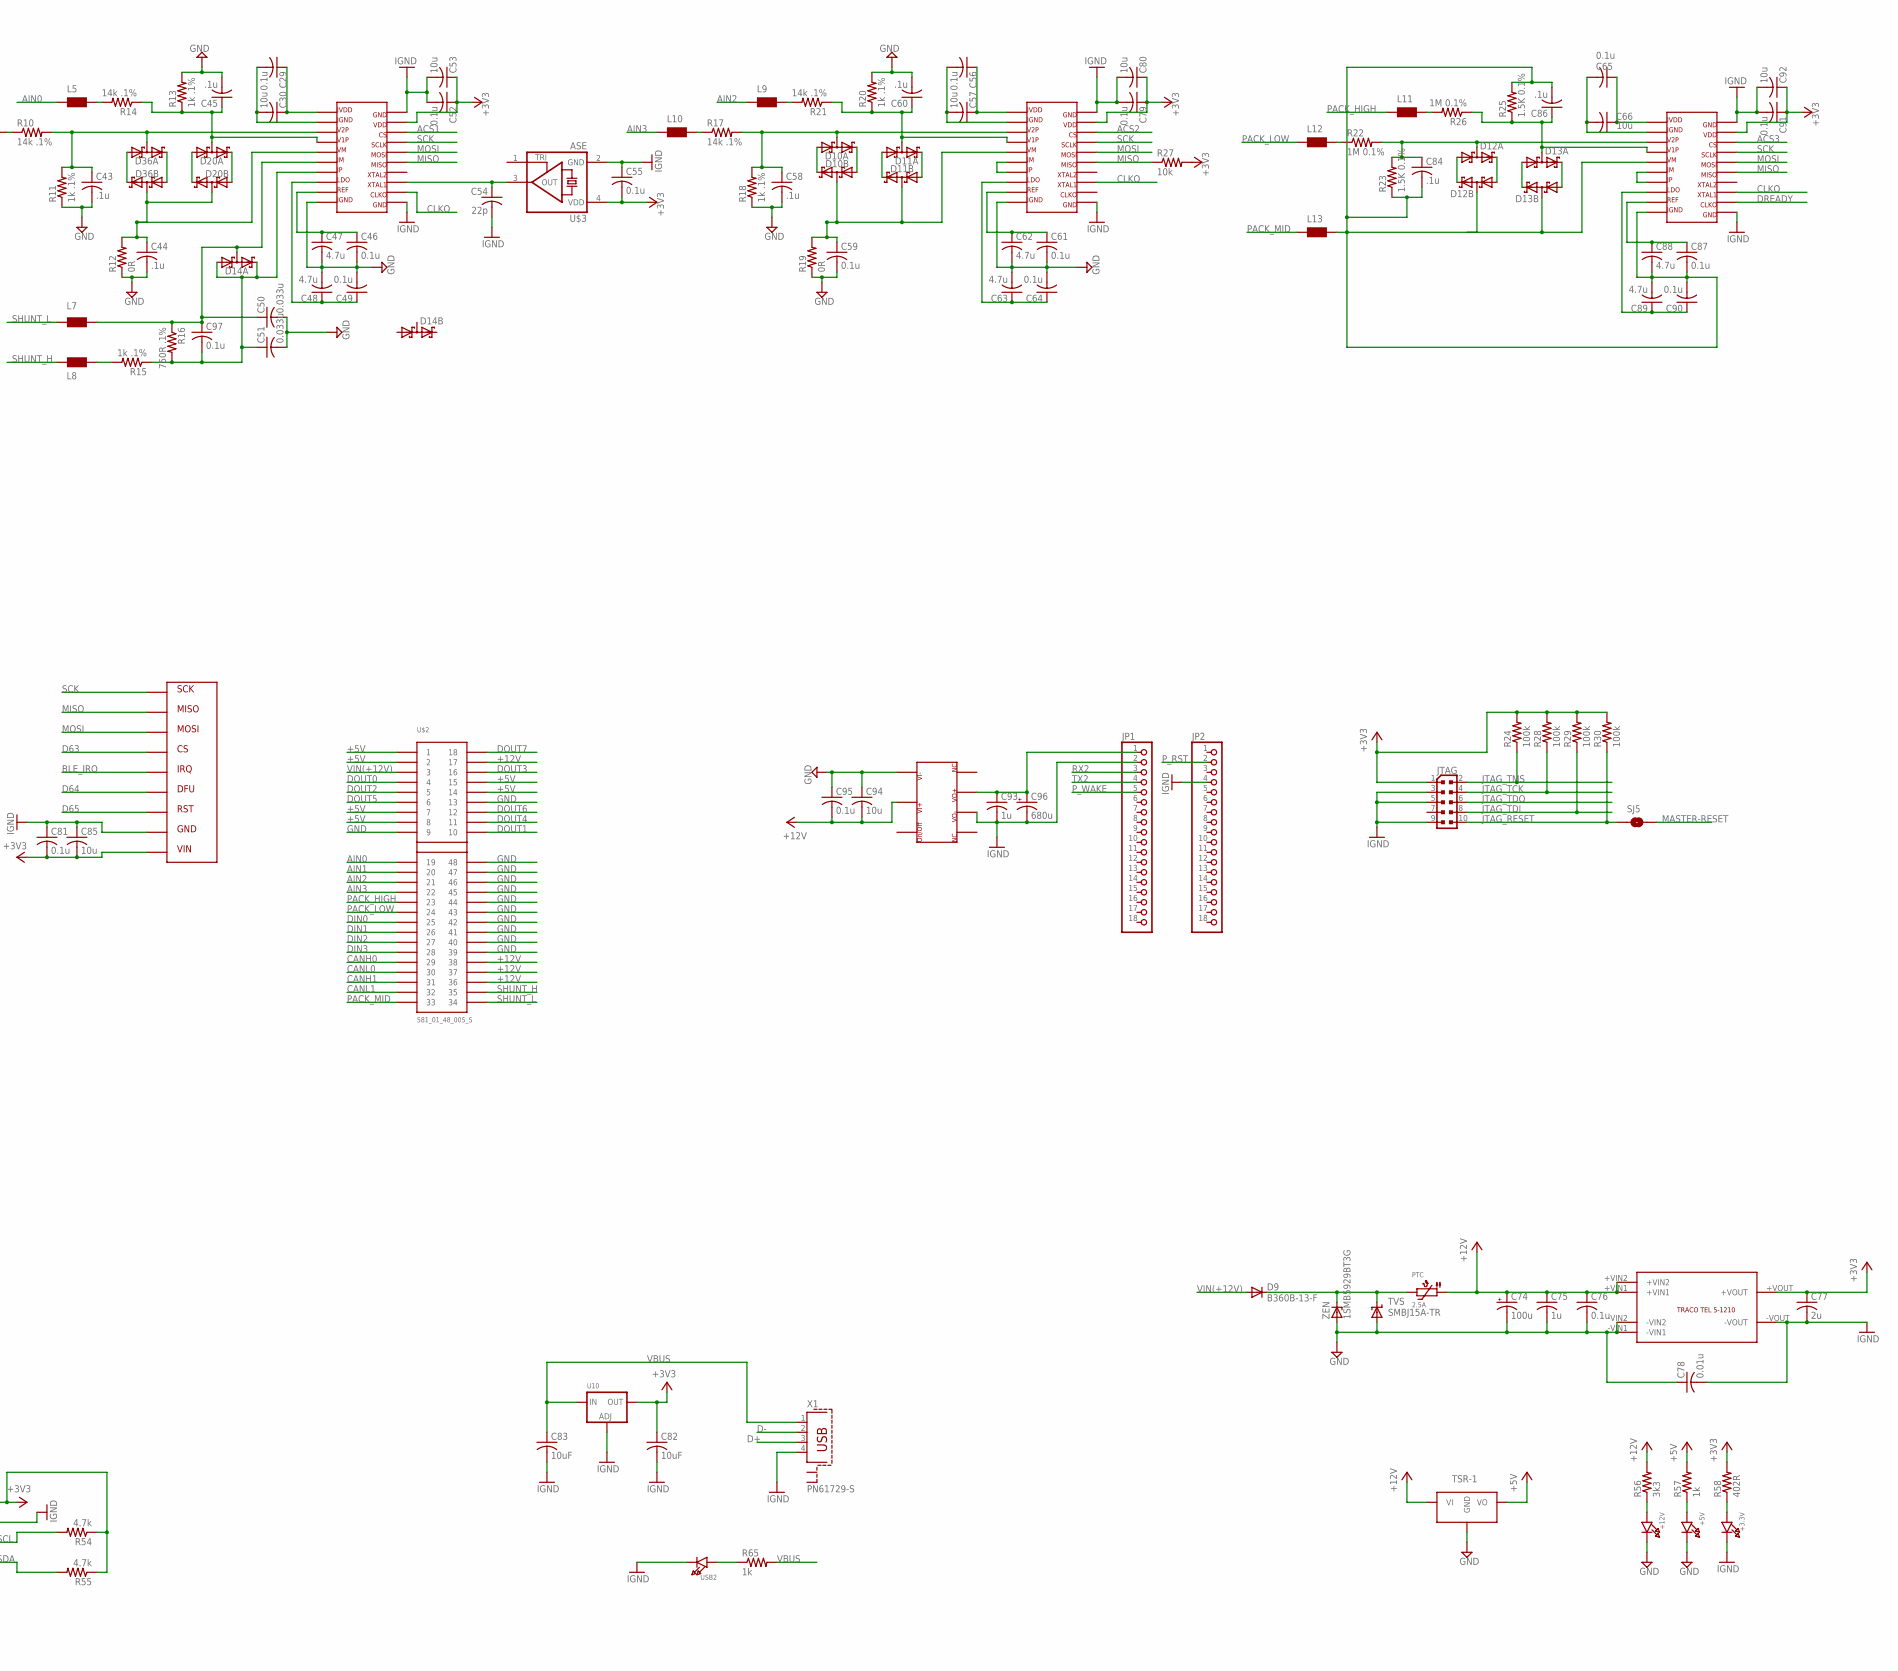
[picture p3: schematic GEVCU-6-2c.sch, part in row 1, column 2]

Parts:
+3.3V, +5V, +12V: LED0805; CHIPLED_0805
C1, C9, C11, C12, C22, C30, C33, C36, C39, C42, C53, C57, C66, C80, C85, C92, C94: 10u; C0805
C2, C3, C4, C5, C6, C7, C8, C10, C13, C14, C15, C16, C17, C18, C19, C20, C21, C29, C31, C32, C34, C35, C37, C38, C40, C41, C46, C49, C52, C55, C56, C59, C61, C64, C65, C67, C68, C70, C71, C73, C76, C79, C81, C87, C90, C91, C95, C97: 0.1u; C0805
C23, C24, C54: 22p; C1206
C25, C26, C27: 22p; C0805
C28: 0.01u; C0805
C43, C44, C45, C58, C60, C84, C86: .1u; C0805
C47, C48, C62, C63, C88, C89: 4.7u; C0805
C50, C51: 0.033u; C0805
C69, C72: 47n; C0805
C74: 100u; E2,5-6
C75, C93: 1u; C0805
C77: 2u; C0805
C78: 0.01u; C1812
C82, C83: 10uF; C0805
C96: 680u; E5-10,5
D1, D2, D3, D4, D5, D6, D7, D8: MBR0520LT; SOD123
D9: B360B-13-F; SMB
D10, D11, D12, D13, D14, D20, D36: BAS70XY; SOT363_PHILIPS
ERASE: PUCHBUTTON
IC9, IC10: ISO1050DW; DUB-R-PDSO-G8
JP1, JP2: PINHD-1X18; 1X18
JTAG: PINHEAD_PINHD-2X5PASSO127; PINHEAD_2X05_127
L1, L2, L3, L4, L5, L6, L7, L8, L9, L10, L11, L12, L13: MH2029-300Y; 0805
LED: LED0805; CHIPLED_0805
OK1, OK2: ILD213; SOIC08
PTC, PTC0, PTC1, PTC2, PTC3, PTC4, PTC5, PTC6, PTC7: 2.5A; PTC1812
R1, R24, R28, R29, R30: 100k; R0805
R2, R3: 39R 1%; R0805
R4: 6k8 1%; R0805
R5, R58: 402R; R0805
R6, R7, R8, R9, R74, R75, R76, R77: 10; R0805
R10, R14, R17, R21: 14k .1%; R0805
R11, R13, R15, R18, R20: 1k .1%; R0805
R12, R19: 0R; R0805
R16: 750R .1%; R0805
R22, R26: 1M 0.1%; R1206
R23, R25: 1.5K 0.1%; R0805
R27, R42, R43, R48, R49, R66, R67, R68, R69, R70, R71, R72, R73: 10k; R0805
R38, R39, R40, R41: 60R; R0805
R44, R45, R46, R47, R50, R51, R52, R53, R57, R65: 1k; R0805
R54, R55: 4.7k; R0805
R56: 3k3; R0805
RESET: PUCHBUTTON
SJ5: SOLDERJUMPERNO; SJ_2S-NO
T2, T4, T5, T6, T7, T8, T10, T12: NMOSSOT223; SOT223
TVS: SMBJ15A-TR; SMBJ
U1: ATSAM3X8EA-AU; LQFP144
U3, U4, U5, U6: ADUM3221BRZ; SOIC127P600X175-8N
U7: CK_CUSTOM_M24M02-DRMN6TP; CK_CUSTOM_SOIC8
U8: TRACO
U9: TSR-1
U10: LM1117SOT223-WAVE; SOT223-W
U11, U12, U24: ADE7913; SOIC20
U$1: CINCON5V
U$2: 581_01_48_005_S
U$3: ASE
U$4: BLE_SPI
USB2: LED0805; CHIPLED_0805
X1: PN61729-S
Y1: 12MHz KX-7 20pF; CRYSTAL-3.2-2.5
Y2: 32.768Khz; ARDUINO_WIFI_SHIELD_V018_TG_RESONATOR_EPSON_FC_145
ZEN: 1SMB5929BT3G; SMB

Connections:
+3V3: C1.1, C2.1, C3.1, C4.1, C5.1, C6.1, C7.1, C19.1, C28.1, C31.1, C34.1, C37.1, C40.1, C52.1, C53.1, C55.2, C67.1, C70.1, C73.1, C77.1, C79.1, C80.1, C81.2, C82.1, C85.2, C91.1, C92.1, ERASE.P$2, IC9.1 (VCC1), IC10.1 (VCC1), JTAG.1, L1.1, L2.1, L3.1, R1.2, R24.2, R27.2, R28.2, R29.2, R30.2, R42.2, R43.2, R48.2, R49.2, R54.1, R55.1, R58.2, U1.11 (VDDIO1), U1.52 (VDDBU), U1.57 (VDDIN), U1.62 (VDDIO2), U1.105 (VDDIO3), U1.125 (VDDIO4), U3.1 (VDD1), U4.1 (VDD1), U5.1 (VDD1), U6.1 (VDD1), U7.PIN8 (VCC), U8.+VOUT, U10.2 (OUT), U11.19, U12.19, U24.19, U$3.4 (VDD), U$4.P$9
+5V: C68.1, C71.1, IC9.9 (VCC2), IC10.9 (VCC2), R57.2, U9.P$3 (VO), U$2.P$1 (1), U$2.P$2 (2), U$2.P$7 (7), U$2.P$8 (8), U$2.P$14 (14), U$2.P$15 (15)
+12V: C32.1, C33.1, C35.1, C36.1, C38.1, C39.1, C41.1, C42.1, C74.+, C75.1, C76.1, C94.2, C95.2, PTC.P$1 (1), R56.2, U3.8 (VDD2), U4.8 (VDD2), U5.8 (VDD2), U6.8 (VDD2), U8.+VIN1, U8.+VIN2, U9.P$1 (VI), U$1.P$2, U$2.P$17 (17), U$2.P$36 (36), U$2.P$37 (37), U$2.P$38 (38)
A0: U1.78 (PA16)
A1: U1.79 (PA24)
A2: U1.80 (PA23)
A3: U1.81 (PA22)
ACS1: U1.14 (PD1), U11.18
ACS2: U1.16 (PD3), U12.18
ACS3: U1.22 (PD9), U24.18
AIN0: L5.1, U$2.P$19 (19)
AIN1: L6.1, U$2.P$20 (20)
AIN2: L9.1, U$2.P$21 (21)
AIN3: L10.1, U$2.P$22 (22)
AVREF: C20.1, L3.2, U1.75 (ADVREF)
BLE_IRQ: U1.15 (PD2), U$4.P$5
CANH0: IC9.12 (CANH), R38.2, U$2.P$29 (29)
CANH1: IC10.12 (CANH), R40.2, U$2.P$31 (31)
CANL0: IC9.13 (CANL), R39.2, U$2.P$30 (30)
CANL1: IC10.13 (CANL), R41.2, U$2.P$32 (32)
CANRX0: IC9.3 (RXD), U1.24 (PA1)
CANRX1: IC10.3 (RXD), U1.76 (PB15)
CANTX0: IC9.6 (TXD), U1.23 (PA0)
CANTX1: IC10.6 (TXD), U1.140 (PB14)
CLKO: U11.12, U12.13, U24.13
D2: R67.2, U1.144 (PB25), U4.3 (VIB)
D3: R66.2, U1.139 (PC28), U4.2 (VIA)
D4: R69.2, U1.137 (PC26), U6.3 (VIB)
D5: R68.2, U1.136 (PC25), U6.2 (VIA)
D6: R71.2, U1.135 (PC24), U5.3 (VIB)
D7: R70.2, U1.134 (PC23), U5.2 (VIA)
D8: R73.2, U1.133 (PC22), U3.3 (VIB)
D9: R72.2, U1.132 (PC21), U3.2 (VIA)
D10: U1.102 (PC29)
D13: R5.2, U1.68 (PB27)
D18: U1.4 (PA11)
D42: U1.71 (PA19)
D48: R42.1, R45.2, U1.97 (PC15)
D49: R43.1, R47.2, U1.96 (PC14)
D50: R48.1, R51.2, U1.95 (PC13)
D51: R49.1, R53.2, U1.94 (PC12)
D63: U1.89 (PB18), U$4.P$4
D64: U1.90 (PB19), U$4.P$6
D65: U1.91 (PB20), U$4.P$7
D+: R3.1, U1.37 (DHSDP), X1.3
D-: R2.1, U1.38 (DHSDM), X1.2
DIN0: R44.1, U$2.P$25 (25)
DIN1: R46.1, U$2.P$26 (26)
DIN2: R50.1, U$2.P$27 (27)
DIN3: R52.1, U$2.P$28 (28)
DOUT0: PTC0.P$1 (1), U$2.P$4 (4)
DOUT1: PTC1.P$1 (1), U$2.P$10 (10)
DOUT2: PTC2.P$1 (1), U$2.P$5 (5)
DOUT3: PTC3.P$1 (1), U$2.P$16 (16)
DOUT4: PTC4.P$1 (1), U$2.P$11 (11)
DOUT5: PTC5.P$1 (1), U$2.P$6 (6)
DOUT6: PTC6.P$1 (1), U$2.P$12 (12)
DOUT7: PTC7.P$1 (1), U$2.P$18 (18)
DREADY: U1.32 (PD10), U24.12
ERASE_S: ERASE.P$1, U1.130 (PC0)
GND: +5V.C, +12V.C, C32.2, C33.2, C35.2, C36.2, C38.2, C39.2, C41.2, C42.2, C43.2, C44.2, C45.2, C46.2, C47.2, C48.2, C49.2, C50.2, C51.2, C58.2, C59.2, C60.2, C61.2, C62.2, C63.2, C64.2, C68.2, C69.2, C71.2, C72.2, C74.-, C75.2, C76.2, C78.1, C94.1, C95.1, D1.A, D2.A, D3.A, D4.A, D5.A, D6.A, D7.A, D8.A, IC9.10 (GND2), IC9.15 (GND2), IC9.16 (GND2), IC10.10 (GND2), IC10.15 (GND2), IC10.16 (GND2), OK1.2 (C), OK1.4 (C), OK2.2 (C), OK2.4 (C), R11.1, R12.1, R13.2, R18.1, R19.1, R20.2, T2.3 (S), T4.3 (S), T5.3 (S), T6.3 (S), T7.3 (S), T8.3 (S), T10.3 (S), T12.3 (S), TVS.A, U3.5 (GND2), U4.5 (GND2), U5.5 (GND2), U6.5 (GND2), U8.-VIN1, U8.-VIN2, U9.P$2 (GND), U11.10, U12.10, U$1.P$1, U$2.P$9 (9), U$2.P$13 (13), U$2.P$39 (39), U$2.P$40 (40), U$2.P$41 (41), U$2.P$42 (42), U$2.P$43 (43), U$2.P$44 (44), U$2.P$45 (45), U$2.P$46 (46), U$2.P$47 (47), U$2.P$48 (48), ZEN.A
IGND: +3.3V.C, C1.2, C2.2, C3.2, C4.2, C5.2, C6.2, C7.2, C8.2, C9.2, C10.2, C11.2, C12.2, C13.2, C14.2, C15.2, C16.2, C17.2, C18.2, C19.2, C20.2, C21.2, C22.2, C23.2, C24.2, C25.2, C26.2, C27.2, C31.2, C34.2, C37.2, C40.2, C52.2, C53.2, C54.2, C55.1, C67.2, C70.2, C73.2, C77.2, C78.2, C79.2, C80.2, C81.1, C82.2, C83.2, C85.1, C91.2, C92.2, C93.2, C96.-, IC9.2 (GND1), IC9.7 (GND1), IC9.8 (GND1), IC10.2 (GND1), IC10.7 (GND1), IC10.8 (GND1), JP1.2, JP2.4, JTAG.3, JTAG.5, JTAG.9, LED.C, OK1.5 (EMIT), OK1.7 (EMIT), OK2.5 (EMIT), OK2.7 (EMIT), R4.1, R66.1, R67.1, R68.1, R69.1, R70.1, R71.1, R72.1, R73.1, RESET.P$1, U1.12 (GND1), U1.33 (GNDPLL), U1.44 (GNDUTMI), U1.46 (JTAGSEL), U1.54 (GNDBU), U1.58 (GND2), U1.74 (GNDANA), U1.106 (GND3), U1.126 (GND4), U3.4 (GND1), U4.4 (GND1), U5.4 (GND1), U6.4 (GND1), U7.PIN1 (NA1), U7.PIN2 (NA2), U7.PIN3 (E2), U7.PIN4 (VSS), U7.PIN7 (WC), U8.-VOUT, U10.1 (ADJ), U11.11, U11.20, U12.11, U12.20, U24.11, U24.20, U$1.P$6, U$3.2 (GND), U$4.P$8, USB2.C, X1.4, Y1.2 (GND), Y1.4 (GND)
JTAG_RESET: JTAG.10, R30.1, SJ5.1
JTAG_TCK: JTAG.4, R28.1, U1.28 (PB28)
JTAG_TDI: JTAG.8, R29.1, U1.29 (PB29)
JTAG_TDO: JTAG.6, U1.30 (PB30)
JTAG_TMS: JTAG.2, R24.1, U1.31 (PB31)
MASTER-RESET: C28.2, RESET.P$2, SJ5.2, U1.47 (NRSTB)
MDRIVE0: R76.2, U6.6 (VOB)
MDRIVE1: R77.2, U6.7 (VOA)
MDRIVE2: R75.2, U5.6 (VOB)
MDRIVE3: R74.2, U5.7 (VOA)
MDRIVE4: R9.2, U4.6 (VOB)
MDRIVE5: R8.2, U4.7 (VOA)
MDRIVE6: R6.2, U3.6 (VOB)
MDRIVE7: R7.2, U3.7 (VOA)
MISO: R27.1, U1.108 (PA25), U11.15, U12.15, U24.15, U$4.P$2
MOSI: U1.109 (PA26), U11.16, U12.16, U24.16, U$4.P$3
unnamed: D36.1 (A1), D36.5 (C2)
unnamed: +3.3V.A, R58.1
unnamed: D9.C, PTC.P$2 (2), TVS.C, ZEN.C
unnamed: +5V.A, R57.1
unnamed: C29.1, C30.1, U11.1
unnamed: LED.A, R5.1
unnamed: L8.1, R15.2
unnamed: D36.2 (C2), D36.4 (A1)
unnamed: C45.1, D20.6 (C1A2), R13.1, R14.1, U11.4
unnamed: C29.2, C30.2, U11.2
unnamed: C43.1, D36.6 (C1A2), R10.2, R11.2, U11.3
unnamed: L5.2, R14.2
unnamed: C44.1, D20.3 (C1A2), D36.3 (C1A2), R12.2, U11.5
unnamed: C65.1, C66.1, U24.1
unnamed: C46.1, C47.1, U11.9
unnamed: C48.1, C49.1, U11.8
unnamed: L6.2, R10.1
unnamed: D20.1 (A1), D20.5 (C2)
unnamed: D20.2 (C2), D20.4 (A1)
unnamed: C51.1, C97.2, D14.1 (A1), D14.2 (C2), R15.1, R16.2, U11.7
unnamed: C50.1, C97.1, D14.6 (C1A2), L7.1, R16.1, U11.6
unnamed: C56.1, C57.1, U12.1
unnamed: C69.1, R38.1, R39.1
unnamed: C72.1, R40.1, R41.1
unnamed: OK1.1 (A), R44.2
unnamed: OK1.3 (A), R46.2
unnamed: OK1.8 (COL), R45.1
unnamed: OK1.6 (COL), R47.1
unnamed: C56.2, C57.2, U12.2
unnamed: OK2.6 (COL), R53.1
unnamed: D10.1 (A1), D10.5 (C2)
unnamed: OK2.8 (COL), R51.1
unnamed: C65.2, C66.2, U24.2
unnamed: OK2.1 (A), R50.2
unnamed: C54.1, U11.13, U$3.3 (OUT)
unnamed: OK2.3 (A), R52.2
unnamed: +12V.A, R56.1
unnamed: D10.2 (C2), D10.4 (A1)
unnamed: D2.C, PTC1.P$2 (2), T2.2 (D), T2.4 (D)
unnamed: C58.1, D10.6 (C1A2), R17.2, R18.2, U12.3
unnamed: D11.1 (A1), D11.5 (C2)
unnamed: D3.C, PTC2.P$2 (2), T4.2 (D), T4.4 (D)
unnamed: D11.2 (C2), D11.4 (A1)
unnamed: R2.2, U1.43 (DFSDM)
unnamed: C59.1, D10.3 (C1A2), D11.3 (C1A2), R19.2, U12.5
unnamed: C60.1, D11.6 (C1A2), R20.1, R21.1, U12.4
unnamed: R3.2, U1.42 (DFSDP)
unnamed: D5.C, PTC4.P$2 (2), T5.2 (D), T5.4 (D)
unnamed: D6.C, PTC5.P$2 (2), T6.2 (D), T6.4 (D)
unnamed: R1.1, U1.53 (FWUP)
unnamed: D7.C, PTC6.P$2 (2), T7.2 (D), T7.4 (D)
unnamed: D8.C, PTC7.P$2 (2), T8.2 (D), T8.4 (D)
unnamed: D4.C, PTC3.P$2 (2), T12.2 (D), T12.4 (D)
unnamed: D1.C, PTC0.P$2 (2), T10.2 (D), T10.4 (D)
unnamed: D12.1 (A1), D12.5 (C2)
unnamed: C61.1, C62.1, U12.9
unnamed: R65.1, USB2.A
unnamed: R6.1, T7.1 (G)
unnamed: R76.1, T10.1 (G)
unnamed: R77.1, T2.1 (G)
unnamed: R74.1, T12.1 (G)
unnamed: R75.1, T4.1 (G)
unnamed: R9.1, T5.1 (G)
unnamed: R8.1, T6.1 (G)
unnamed: R7.1, T8.1 (G)
unnamed: C63.1, C64.1, U12.8
unnamed: L9.2, R21.2
unnamed: L10.2, R17.1
unnamed: U12.6, U12.7
unnamed: D12.2 (C2), D12.4 (A1)
unnamed: C84.1, D12.6 (C1A2), R22.2, R23.2, U24.3
unnamed: D13.1 (A1), D13.5 (C2)
unnamed: D13.2 (C2), D13.4 (A1)
unnamed: D13.3 (C1A2), U24.5
unnamed: C86.1, D13.6 (C1A2), R25.1, R26.1, U24.4
unnamed: C87.1, C88.1, U24.9
unnamed: C89.1, C90.1, U24.8
unnamed: L11.2, R26.2
unnamed: L12.2, R22.1
unnamed: U24.6, U24.7
unnamed: C93.1, C96.+, JP1.1, U$1.P$5
unnamed: C84.2, C86.2, C87.2, C88.2, C89.2, C90.2, D12.3 (C1A2), L13.2, R23.1, R25.2, U24.10
PACK_HIGH: L11.1, U$2.P$23 (23)
PACK_LOW: L12.1, U$2.P$24 (24)
PACK_MID: L13.1, U$2.P$33 (33)
P_RST: JP2.2, U1.66 (PC8)
P_WAKE: JP1.5, U1.65 (PC7)
RX0: U1.27 (PA8)
RX2: JP1.3, U1.5 (PA12)
RX3: U1.18 (PD5)
SCK: U1.110 (PA27), U11.17, U12.17, U24.17, U$4.P$1
SCL: R54.2, U1.87 (PB13), U7.PIN6 (SCL)
SDA: R55.2, U1.86 (PB12), U7.PIN5 (SDA)
SHUNT_H: L8.2, U$2.P$35 (35)
SHUNT_L: L7.2, U$2.P$34 (34)
TX0: U1.2 (PA9)
TX2: JP1.4, U1.6 (PA13)
TX3: U1.17 (PD4)
VBG: C27.1, R4.2, U1.40 (VBG)
VBUS: C83.1, R65.2, U1.39 (VBUS), U10.3 (IN), X1.1
VDDANA: C10.1, C11.1, L1.2, U1.73 (VDDANA)
VDDOUT: C12.1, C13.1, C14.1, C15.1, C16.1, C17.1, C18.1, L4.1, U1.10 (VDDCORE1), U1.45 (VDDCORE2), U1.56 (VDDOUT), U1.61 (VDDCORE3), U1.104 (VDDCORE4), U1.124 (VDDCORE5)
VDDOUTMI: C8.1, C9.1, L2.2, U1.41 (VDDUTMI)
VDDPLL: C21.1, C22.1, L4.2, U1.34 (VDDPLL)
VIN(+12V): D9.A, U$2.P$3 (3)
XIN: C24.1, U1.36 (XIN), Y1.1 (C1)
XIN32: C26.1, U1.48 (XIN32), Y2.P$2 (2)
XOUT: C23.1, U1.35 (XOUT), Y1.3 (C2)
XOUT32: C25.1, U1.49 (XOUT32), Y2.P$1 (1)

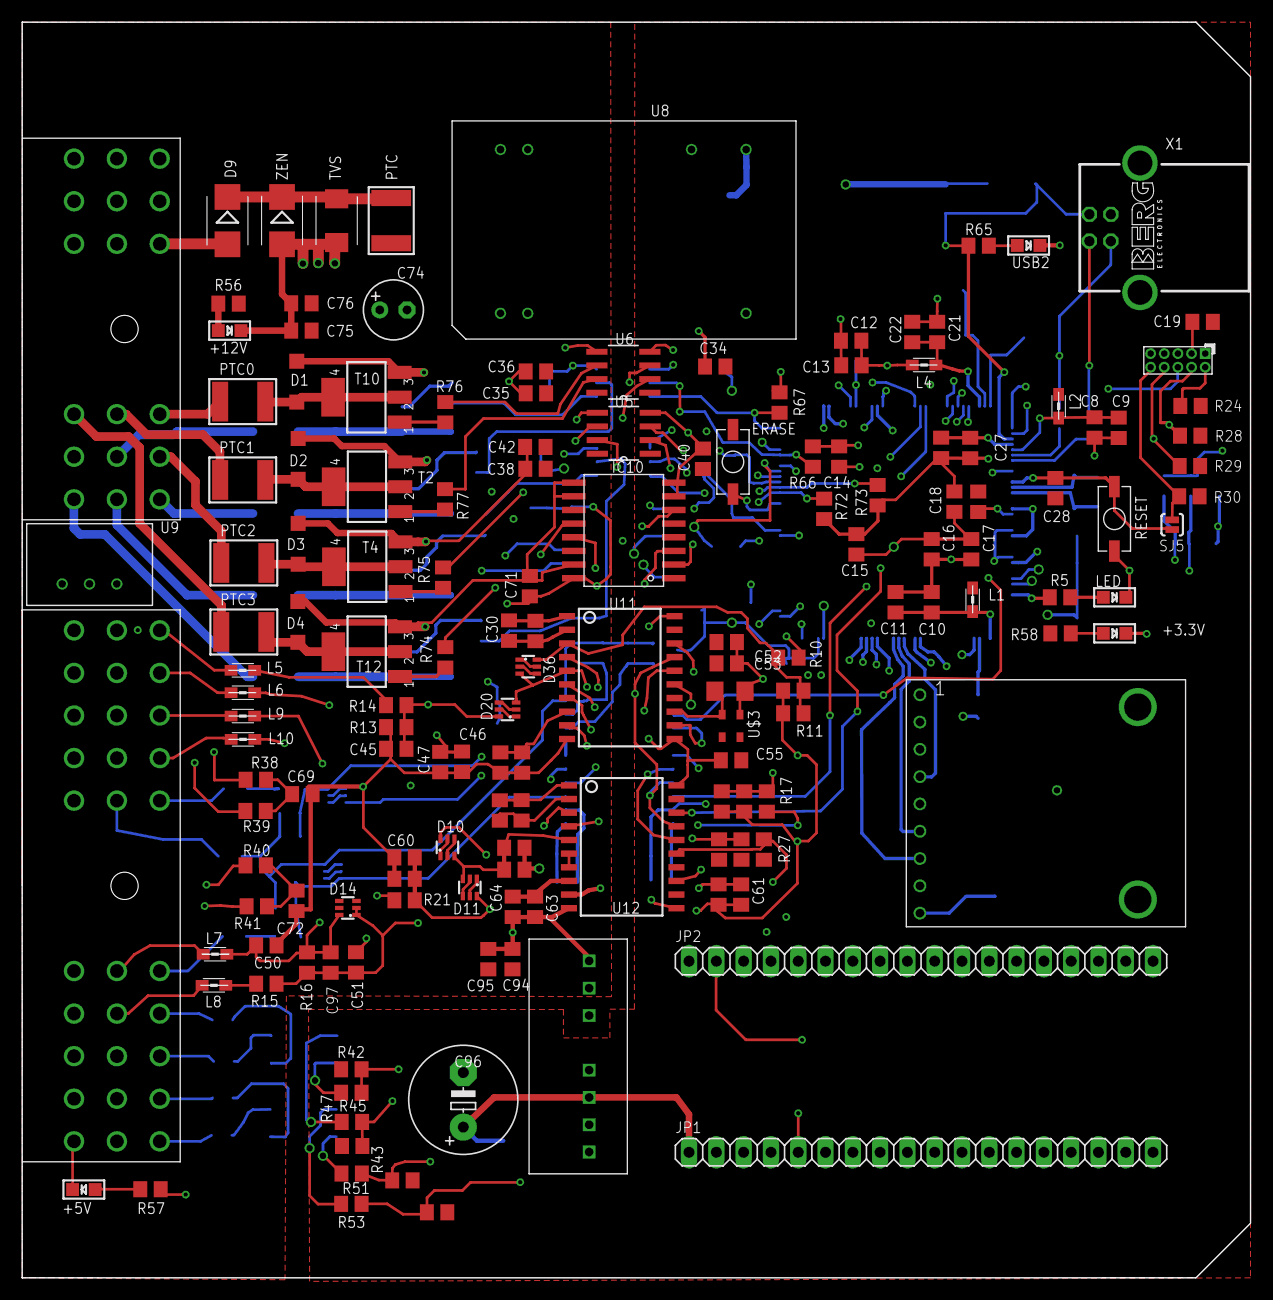
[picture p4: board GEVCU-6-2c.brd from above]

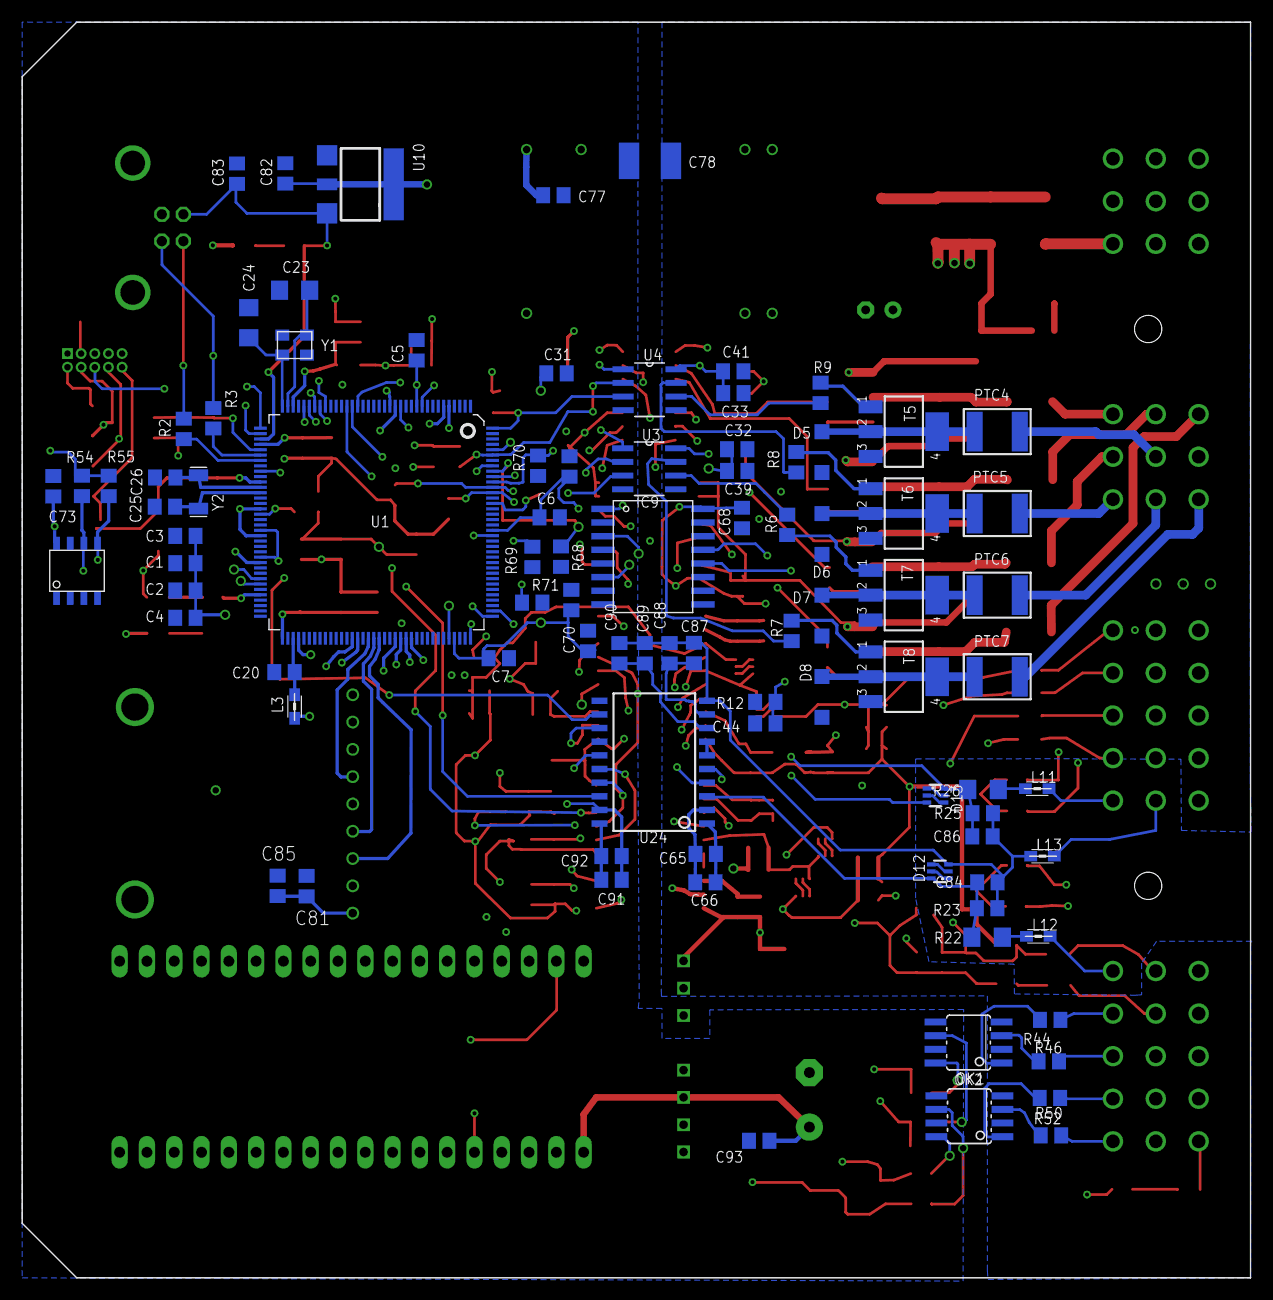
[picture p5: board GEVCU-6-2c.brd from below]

Board: 4 copper layers, 114.3 x 116.8 mm, 243 parts (90 on the bottom side), 176 nets.

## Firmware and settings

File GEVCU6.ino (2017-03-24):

/*
 GEVCU6.ino
 New hardware version 9/20/2016 for Hardware 6.23c
 Created: 1/4/2013 1:34:14 PM
 Author: Collin Kidder
 
 New, new plan: Allow for an arbitrary # of devices that can have both tick and canbus handlers. These devices register themselves
 into the handler framework and specify which sort of device they are. They can have custom tick intervals and custom can filters.
 The system automatically manages when to call the tick handlers and automatically filters canbus and sends frames to the devices.
 There is a facility to send data between devices by targetting a certain type of device. For instance, a motor controller
 can ask for any throttles and then retrieve the current throttle position from them.

Copyright (c) 2013 Collin Kidder, Michael Neuweiler, Charles Galpin

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
 */
 
/*Changelog removed. All changes are logged to GIT */

/*
Random comments on things that should be coded up soon:
4. It is a possibility that there should be support for actually controlling the power to some of the devices.
	For instance, power could be controlled to the +12V connection at the DMOC so that it can be power cycled
	in software. But, that uses up an input and people can just cycle the key (though that resets the GEVCU too)
5. Some people (like me, Collin) have a terrible habit of mixing several coding styles. It would be beneficial to
	continue to harmonize the source code - Perhaps use a tool to do this.
6. It should be possible to limit speed and/or torque in reverse so someone doesn't kill themselves or someone else
	while gunning it in reverse - The configuration variable is there and settable now. Just need to integrate it.
7. The DMOC code duplicates a bunch of functionality that the base class also used to implement. We've got to figure
	out where the overlaps are and fix it up so that as much as possible is done generically at the base MotorController
	class and not directly in the Dmoc class.
*/

#include "GEVCU.h"

// The following includes are required in the .ino file by the Arduino IDE in order to properly
// identify the required libraries for the build.
#include <due_rtc.h>
#include <due_can.h>
#include <FirmwareReceiver.h>
#include <due_wire.h>
#include <DueTimer.h>
#include <SPI.h>

//RTC_clock rtc_clock(XTAL); //init RTC with the external 32k crystal as a reference

//Evil, global variables
PrefHandler *sysPrefs;
MemCache *memCache;
Heartbeat *heartbeat;
SerialConsole *serialConsole;
Device *btDevice;
template<class T> inline Print &operator <<(Print &obj, T arg) { obj.print(arg); return obj; } //Lets us stream SerialUSB

byte i = 0;

//initializes all the system EEPROM values. Chances are this should be broken out a bit but
//there is only one checksum check for all of them so it's simple to do it all here.

void initSysEEPROM() {
	//three temporary storage places to make saving to EEPROM easy
	uint8_t eight;
	uint16_t sixteen;
	uint32_t thirtytwo;

	eight = 6; //GEVCU 6.2 board
	sysPrefs->write(EESYS_SYSTEM_TYPE, eight);

	sixteen = 1024; //no gain
	sysPrefs->write(EESYS_ADC0_GAIN, sixteen);
	sysPrefs->write(EESYS_ADC1_GAIN, sixteen);
	sysPrefs->write(EESYS_ADC2_GAIN, sixteen);
	sysPrefs->write(EESYS_ADC3_GAIN, sixteen);

	sixteen = 0; //no offset
	sysPrefs->write(EESYS_ADC0_OFFSET, sixteen);
	sysPrefs->write(EESYS_ADC1_OFFSET, sixteen);
	sysPrefs->write(EESYS_ADC2_OFFSET, sixteen);
	sysPrefs->write(EESYS_ADC3_OFFSET, sixteen);

	sixteen = 500; //multiplied by 1000 so 500k baud
	sysPrefs->write(EESYS_CAN0_BAUD, sixteen);
	sysPrefs->write(EESYS_CAN1_BAUD, sixteen);

	eight = 3;  //0=debug, 1=info,2=warn,3=error,4=off
	sysPrefs->write(EESYS_LOG_LEVEL, eight);

	sysPrefs->saveChecksum();
}

void createObjects() {
	PotThrottle *paccelerator = new PotThrottle();
	CanThrottle *caccelerator = new CanThrottle();
	PotBrake *pbrake = new PotBrake();
    TestThrottle *testAccel = new TestThrottle();
	CanBrake *cbrake = new CanBrake();
	DmocMotorController *dmotorController = new DmocMotorController();
    CodaMotorController *cmotorController = new CodaMotorController();
	CKMotorController *ckMotorController = new CKMotorController();
	RMSMotorController *rmsMotorController = new RMSMotorController();
    TestMotorController *testMotorController = new TestMotorController();
    DCDCController *dcdcController = new DCDCController();
	BrusaMotorController *bmotorController = new BrusaMotorController();
	ThinkBatteryManager *BMS = new ThinkBatteryManager();
	ELM327Emu *emu = new ELM327Emu();
    ADAFRUITBLE *ble = new ADAFRUITBLE();
    EVIC *eVIC = new EVIC();
    PowerkeyPad *powerKey = new PowerkeyPad();
    VehicleSpecific *vehicleSpecific = new VehicleSpecific();
}

void initializeDevices() {
	//heartbeat is always enabled now
	heartbeat = new Heartbeat();
	Logger::info("add: Heartbeat (id: %X, %X)", HEARTBEAT, heartbeat);
	heartbeat->setup();

	//fault handler is always enabled too - its also statically allocated so no using -> here
	//This is initialized before the other devices so that they can go ahead and use it if they fault upon start up
	faultHandler.setup();

	/*
	We used to instantiate all the objects here along with other code. To simplify things this is done somewhat
	automatically now. Just instantiate your new device object in createObjects above. This takes care of the details
	so long as you follow the template of how other devices were coded.
	*/
	createObjects(); 

	/*
	 *	We defer setting up the devices until here. This allows all objects to be instantiated
	 *	before any of them set up. That in turn allows the devices to inspect what else is
	 *	out there as they initialize. For instance, a motor controller could see if a BMS
	 *	exists and supports a function that the motor controller wants to access.
	 */
	deviceManager.sendMessage(DEVICE_ANY, INVALID, MSG_STARTUP, NULL);

}

void setup() {
    //Most boards pre 6.2 have outputs on 2-9 and a problem where their outputs can trigger on for just a quick moment
    //upon start up. So, try to pull the outputs low as soon as we can just to be sure.
    for (int i = 2; i < 10; i++) {
        pinMode(i, OUTPUT);
        digitalWrite(i, LOW);
    }
    
    pinMode(64, OUTPUT); //DFU for BLE Module
    digitalWrite(64, HIGH);
    pinMode(65, OUTPUT); //reset for BLE module
    digitalWrite(65, HIGH);
	
    //delay(5000);  //This delay lets you see startup.  But it breaks DMOC645 really badly.  You have to have comm way before 5 seconds.
    
    //SerialUSB.println(millis());
       
	pinMode(BLINK_LED, OUTPUT);
	digitalWrite(BLINK_LED, LOW);
    SerialUSB.begin(CFG_SERIAL_SPEED);
	SerialUSB.println(CFG_VERSION);
	SerialUSB.print("Build number: ");
	SerialUSB.println(CFG_BUILD_NUM);
	Wire.begin((uint32_t)1000000);
	Logger::info("TWI init ok");
	memCache = new MemCache();
	Logger::info("add MemCache (id: %X, %X)", MEMCACHE, memCache);
	memCache->setup();
	sysPrefs = new PrefHandler(SYSTEM);
	if (!sysPrefs->checksumValid()) 
        {
	      Logger::info("Initializing system EEPROM settings");
	      initSysEEPROM();
	    } 
        else {Logger::info("Using existing EEPROM system values");}//checksum is good, read in the values stored in EEPROM

	uint8_t loglevel;
	sysPrefs->read(EESYS_LOG_LEVEL, &loglevel);
	//loglevel = 0; //force debugging log level
    Logger::console("LogLevel: %i", loglevel);
	Logger::setLoglevel((Logger::LogLevel)loglevel);    
	systemIO.setup();  
	canHandlerEv.setup();
	canHandlerCar.setup();
	Logger::info("SYSIO init ok");	

	initializeDevices();
    serialConsole = new SerialConsole(memCache, heartbeat);
	serialConsole->printMenu();
	btDevice = deviceManager.getDeviceByID(ELM327EMU);
    deviceManager.sendMessage(DEVICE_WIFI, ADABLUE, MSG_CONFIG_CHANGE, NULL); //Load config into BLE interface
	Logger::info("System Ready");	
}

void loop() {
#ifdef CFG_TIMER_USE_QUEUING
	tickHandler.process();
#endif

	// check if incoming frames are available in the can buffer and process them
	canHandlerEv.process();
	canHandlerCar.process();

	serialConsole->loop();

    systemIO.pollInitialization();
}

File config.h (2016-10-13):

/*
 * config.h
 *
 * Defines the components to be used in the GEVCU and allows the user to configure
 * static parameters.
 *
 * Note: Make sure with all pin defintions of your hardware that each pin number is
 *       only defined once.

 Copyright (c) 2013 Collin Kidder, Michael Neuweiler, Charles Galpin

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
THE SOFTWARE IS PROVIDED "AS IS", WITHOUT WARRANTY OF ANY KIND,
EXPRESS OR IMPLIED, INCLUDING BUT NOT LIMITED TO THE WARRANTIES OF
MERCHANTABILITY, FITNESS FOR A PARTICULAR PURPOSE AND NONINFRINGEMENT.
IN NO EVENT SHALL THE AUTHORS OR COPYRIGHT HOLDERS BE LIABLE FOR ANY
CLAIM, DAMAGES OR OTHER LIABILITY, WHETHER IN AN ACTION OF CONTRACT,
TORT OR OTHERWISE, ARISING FROM, OUT OF OR IN CONNECTION WITH THE
SOFTWARE OR THE USE OR OTHER DEALINGS IN THE SOFTWARE.
 *      Author: Michael Neuweiler
 */

#ifndef CONFIG_H_
#define CONFIG_H_

#include <due_can.h>

#define CFG_BUILD_NUM	1058      //increment this every time a git commit is done. 
#define CFG_VERSION "GEVCU 2016-10-13"

/*
 * SERIAL CONFIGURATION
 */
#define CFG_SERIAL_SPEED 115200
//#define SerialUSB Serial // re-route serial-usb output to programming port ;) comment if output should go to std usb


//The defines that used to be here to configure devices are gone now.
//The EEPROM stores which devices to bring up at start up and all
//devices are programmed into the firware at the same time.

/*
 * TIMER INTERVALS
 *
 * specify the intervals (microseconds) at which each device type should be "ticked"
 * try to use the same numbers for several devices because then they will share
 * the same timer (out of a limited number of 9 timers).
 */
#define CFG_TICK_INTERVAL_HEARTBEAT                 2000000
#define CFG_TICK_INTERVAL_POT_THROTTLE              40000
#define CFG_TICK_INTERVAL_CAN_THROTTLE              40000
#define CFG_TICK_INTERVAL_MOTOR_CONTROLLER          40000
#define CFG_TICK_INTERVAL_MOTOR_CONTROLLER_DMOC     40000
#define CFG_TICK_INTERVAL_MOTOR_CONTROLLER_CODAUQM  10000
#define CFG_TICK_INTERVAL_MOTOR_CONTROLLER_BRUSA    20000
#define CFG_TICK_INTERVAL_MEM_CACHE                 40000
#define CFG_TICK_INTERVAL_BMS_THINK                 500000
#define CFG_TICK_INTERVAL_WIFI                      200000
#define CFG_TICK_INTERVAL_BLE                       40000
#define CFG_TICK_INTERVAL_DCDC                      200000
#define CFG_TICK_INTERVAL_EVIC                      100000
#define CFG_TICK_INTERVAL_VEHICLE                   100000

/*
 * CAN BUS CONFIGURATION
 */
#define CFG_CAN0_SPEED CAN_BPS_500K // specify the speed of the CAN0 bus (EV)
#define CFG_CAN1_SPEED CAN_BPS_500K // specify the speed of the CAN1 bus (Car)
#define CFG_CAN0_NUM_RX_MAILBOXES 9 // amount of CAN bus receive mailboxes for CAN0
#define CFG_CAN1_NUM_RX_MAILBOXES 9 // amount of CAN bus receive mailboxes for CAN1
#define CFG_CANTHROTTLE_MAX_NUM_LOST_MSG 3 // maximum number of lost messages allowed

/*
 * MISCELLANEOUS
 *
 */
#define CFG_THROTTLE_TOLERANCE  150 //the max that things can go over or under the min/max without fault - 1/10% each #


/*
 * HARD CODED PARAMETERS
 *
 * If USE_HARD_CODED is defined or the checksum of the parameters stored in EEPROM,
 * the parameter values defined here are used instead of those stored in the EEPROM.
 */
//#define USE_HARD_CODED
#define ThrottleNumPots			1		//# of pots to use by default
#define ThrottleADC1			0		//Which pin to use
#define ThrottleADC2			1		//Which pin to use
#define ThrottleSubtype			1		//subtype 1 is a standard linear pot throttle
#define ThrottleRegenMinValue	270		//where does Regen stop (1/10 of percent)
#define ThrottleRegenMaxValue	30		//where Regen is at maximum (1/10 of percent)
#define ThrottleFwdValue		300		//where does forward motion start
#define ThrottleMapValue		750		//Where is the 1/2 way point for throttle
#define ThrottleMinRegenValue	0		//how many percent of full power to use at minimal regen
#define ThrottleMaxRegenValue	50		//how many percent of full power to use at maximum regen
#define ThrottleCreepValue		0		//how many percent of full power to use at creep
#define ThrottleMaxErrValue		150		//tenths of percentage allowable deviation between pedals
#define Throttle1MinValue		95		//Value ADC reads when pedal is up
#define Throttle1MaxValue		3150		//Value ADC reads when pedal fully depressed
#define Throttle2MinValue		0		//Value ADC reads when pedal is up
#define Throttle2MaxValue		0	//Value ADC reads when pedal fully depressed
#define BrakeMinValue			100		//Value ADC reads when brake is not pressed
#define BrakeMaxValue			3200		//Value ADC reads when brake is pushed all of the way down
#define BrakeMinRegenValue		0		//percent of full power to use for brake regen (min)
#define BrakeMaxRegenValue		50		//percent of full power to use for brake regen (max)
#define BrakeADC				2       //which ADC pin to use
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

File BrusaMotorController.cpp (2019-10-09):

/*
 * BrusaMotorController.cpp
 *
 *
 Copyright (c) 2013 Collin Kidder, Michael Neuweiler, Charles Galpin

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
 */

#include "BrusaMotorController.h"

/*
 Warning:
 At high speed disable the DMC_EnableRq can be dangerous because a field weakening current is
 needed to achieve zero torque. Switching off the DMC in such a situation will make heavy regenerat-
 ing torque that can't be controlled.
 */

/*
 * Constructor
 */
BrusaMotorController::BrusaMotorController() : MotorController() {
    prefsHandler = new PrefHandler(BRUSA_DMC5);
    torqueAvailable = 0;
    maxPositiveTorque = 0;
    minNegativeTorque = 0;
    limiterStateNumber = 0;

    tickCounter = 0;

    commonName = "Brusa DMC5 Inverter";
}

/*
 * Setup the device if it is enabled in configuration.
 */
void BrusaMotorController::setup() {
    tickHandler.detach(this);

    Logger::info("add device: Brusa DMC5 (id: %X, %X)", BRUSA_DMC5, this);

    loadConfiguration();
    MotorController::setup(); // run the parent class version of this function

    // register ourselves as observer of 0x258-0x268 and 0x458 can frames
    canHandlerEv.attach(this, CAN_MASKED_ID_1, CAN_MASK_1, false);
    canHandlerEv.attach(this, CAN_MASKED_ID_2, CAN_MASK_2, false);

    tickHandler.attach(this, CFG_TICK_INTERVAL_MOTOR_CONTROLLER_BRUSA);
}

/*
 * Process event from the tick handler.
 *
 * The super-class requests desired levels from the throttle and
 * brake and decides which one to apply.
 */
void BrusaMotorController::handleTick() {
    MotorController::handleTick(); // call parent
    tickCounter++;

    sendControl();	// send CTRL every 20ms
    if (tickCounter > 4) {
        sendControl2();	// send CTRL_2 every 100ms
        sendLimits();	// send LIMIT every 100ms
        tickCounter = 0;
    }
}

/*
 * Send DMC_CTRL message to the motor controller.
 *
 * This message controls the power-stage in the controller, clears the error latch
 * in case errors were detected and requests the desired torque / speed.
 */
void BrusaMotorController::sendControl() {
    BrusaMotorControllerConfiguration *config = (BrusaMotorControllerConfiguration *)getConfiguration();
    prepareOutputFrame(CAN_ID_CONTROL);

    speedRequested = 0;
    torqueRequested = 0;

    outputFrame.data.bytes[0] = enablePositiveTorqueSpeed; // | enableNegativeTorqueSpeed;
    if (faulted) {
        outputFrame.data.bytes[0] |= clearErrorLatch;
    } else {
        if ((running || speedActual > 1000) && !systemIO.getDigitalIn(1)) { // see warning about field weakening current to prevent uncontrollable regen
            outputFrame.data.bytes[0] |= enablePowerStage;
        }
        if (running) {
            if (config->enableOscillationLimiter)
                outputFrame.data.bytes[0] |= enableOscillationLimiter;

            if (powerMode == modeSpeed) {
                outputFrame.data.bytes[0] |= enableSpeedMode;
                speedRequested = throttleRequested * config->speedMax / 1000;
                torqueRequested = config->torqueMax; // positive number used for both speed directions
            } else { // torque mode
                speedRequested = config->speedMax; // positive number used for both torque directions
                torqueRequested = throttleRequested * config->torqueMax / 1000;
            }

            // set the speed in rpm
            outputFrame.data.bytes[2] = (speedRequested & 0xFF00) >> 8;
            outputFrame.data.bytes[3] = (speedRequested & 0x00FF);

            // set the torque in 0.01Nm (GEVCU uses 0.1Nm -> multiply by 10)
            outputFrame.data.bytes[4] = ((torqueRequested * 10) & 0xFF00) >> 8;
            outputFrame.data.bytes[5] = ((torqueRequested * 10) & 0x00FF);
        }
    }

    if (Logger::isDebug())
        Logger::debug(BRUSA_DMC5, "requested Speed: %l rpm, requested Torque: %f Nm", speedRequested, (float)torqueRequested/10.0F);

    canHandlerEv.sendFrame(outputFrame);
}

/*
 * Send DMC_CTRL2 message to the motor controller.
 *
 * This message controls the mechanical power limits for motor- and regen-mode.
 */
void BrusaMotorController::sendControl2() {
    BrusaMotorControllerConfiguration *config = (BrusaMotorControllerConfiguration *)getConfiguration();

    prepareOutputFrame(CAN_ID_CONTROL_2);
    outputFrame.data.bytes[0] = ((config->torqueSlewRate * 10) & 0xFF00) >> 8;
    outputFrame.data.bytes[1] = ((config->torqueSlewRate * 10) & 0x00FF);
    outputFrame.data.bytes[2] = (config->speedSlewRate & 0xFF00) >> 8;
    outputFrame.data.bytes[3] = (config->speedSlewRate & 0x00FF);
    outputFrame.data.bytes[4] = (config->maxMechanicalPowerMotor & 0xFF00) >> 8;
    outputFrame.data.bytes[5] = (config->maxMechanicalPowerMotor & 0x00FF);
    outputFrame.data.bytes[6] = (config->maxMechanicalPowerRegen & 0xFF00) >> 8;
    outputFrame.data.bytes[7] = (config->maxMechanicalPowerRegen & 0x00FF);

    canHandlerEv.sendFrame(outputFrame);
}

/*
 * Send DMC_LIM message to the motor controller.
 *
 * This message controls the electrical limits in the controller.
 */
void BrusaMotorController::sendLimits() {
    BrusaMotorControllerConfiguration *config = (BrusaMotorControllerConfiguration *)getConfiguration();

    prepareOutputFrame(CAN_ID_LIMIT);
    outputFrame.data.bytes[0] = (config->dcVoltLimitMotor & 0xFF00) >> 8;
    outputFrame.data.bytes[1] = (config->dcVoltLimitMotor & 0x00FF);
    outputFrame.data.bytes[2] = (config->dcVoltLimitRegen & 0xFF00) >> 8;
    outputFrame.data.bytes[3] = (config->dcVoltLimitRegen & 0x00FF);
    outputFrame.data.bytes[4] = (config->dcCurrentLimitMotor & 0xFF00) >> 8;
    outputFrame.data.bytes[5] = (config->dcCurrentLimitMotor & 0x00FF);
    outputFrame.data.bytes[6] = (config->dcCurrentLimitRegen & 0xFF00) >> 8;
    outputFrame.data.bytes[7] = (config->dcCurrentLimitRegen & 0x00FF);

    canHandlerEv.sendFrame(outputFrame);
}

/*
 * Prepare the CAN transmit frame.
 * Re-sets all parameters in the re-used frame.
 */
void BrusaMotorController::prepareOutputFrame(uint32_t id) {
    outputFrame.length = 8;
    outputFrame.id = id;
    outputFrame.extended = 0;
    outputFrame.rtr = 0;

    outputFrame.data.bytes[1] = 0;
    outputFrame.data.bytes[2] = 0;
    outputFrame.data.bytes[3] = 0;
    outputFrame.data.bytes[4] = 0;
    outputFrame.data.bytes[5] = 0;
    outputFrame.data.bytes[6] = 0;
    outputFrame.data.bytes[7] = 0;
}
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

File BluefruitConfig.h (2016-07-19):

// COMMON SETTINGS
// ----------------------------------------------------------------------------------------------
// These settings are used in both SW UART, HW UART and SPI mode
// ----------------------------------------------------------------------------------------------
#define BUFSIZE                        128   // Size of the read buffer for incoming data
#define VERBOSE_MODE                   false  // If set to 'true' enables debug output


// SOFTWARE UART SETTINGS
// ----------------------------------------------------------------------------------------------
// The following macros declare the pins that will be used for 'SW' serial.
// You should use this option if you are connecting the UART Friend to an UNO
// ----------------------------------------------------------------------------------------------
#define BLUEFRUIT_SWUART_RXD_PIN       9    // Required for software serial!
#define BLUEFRUIT_SWUART_TXD_PIN       10   // Required for software serial!
#define BLUEFRUIT_UART_CTS_PIN         11   // Required for software serial!
#define BLUEFRUIT_UART_RTS_PIN         -1   // Optional, set to -1 if unused


// HARDWARE UART SETTINGS
// ----------------------------------------------------------------------------------------------
// The following macros declare the HW serial port you are using. Uncomment
// this line if you are connecting the BLE to Leonardo/Micro or Flora
// ----------------------------------------------------------------------------------------------
#ifdef Serial1    // this makes it not complain on compilation if there's no Serial1
  #define BLUEFRUIT_HWSERIAL_NAME      Serial
#endif


// SHARED UART SETTINGS
// ----------------------------------------------------------------------------------------------
// The following sets the optional Mode pin, its recommended but not required
// ----------------------------------------------------------------------------------------------
#define BLUEFRUIT_UART_MODE_PIN        -1    // Set to -1 if unused


// SHARED SPI SETTINGS
// ----------------------------------------------------------------------------------------------
// The following macros declare the pins to use for HW and SW SPI communication.
// SCK, MISO and MOSI should be connected to the HW SPI pins on the Uno when
// using HW SPI.  These standard pins are MISO-74, MOSI-75, and SCK-76  
//This should be used with nRF51822 based Bluefruit LE modules
// that use SPI (Bluefruit LE SPI Friend).
// ----------------------------------------------------------------------------------------------
#define BLUEFRUIT_SPI_CS               63
#define BLUEFRUIT_SPI_IRQ              27
#define BLUEFRUIT_SPI_RST              65    // Optional but recommended, set to -1 if unused

// SOFTWARE SPI SETTINGS
// ----------------------------------------------------------------------------------------------
// The following macros declare the pins to use for SW SPI communication.
// This should be used with nRF51822 based Bluefruit LE modules that use SPI
// (Bluefruit LE SPI Friend).
// ----------------------------------------------------------------------------------------------
#define BLUEFRUIT_SPI_SCK              13
#define BLUEFRUIT_SPI_MISO             12
#define BLUEFRUIT_SPI_MOSI             11

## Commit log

2016-07-01 Add support for GEVCU 6.2 boards with the new 24 bit ADC. Add ability to set offset and gain for all analog inputs
2016-07-01 Disable fault handler again (still broken and slow), add routine to automatically determine proper ADC offsets
    [SerialConsole.cpp]
2016-07-12 Add support for custom motor controller board driving DMOC645 power section, add firmware receiver but commented out for now, updated version number, add GEVCU6.2 board files and BOM
    [GEVCU-6-2c.brd, GEVCU-6-2c.sch, GEVCU-6_BOM.xlsx]
2016-07-18 Fixes on GEVCU board files, addition of an Eagle library that contains some of the parts on the GEVCU board.
    [GEVCU-6-2c.brd, GEVCU-6-2c.sch]
2016-07-19 Update GEVCU6 BOM, add parts list for GEVCU6, remove some ancient boards
    [Analog_Board.brd, Analog_Board.sch, Analog_Shield.brd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]
2016-07-22 Switched to sending structs instead of individual values since BLE module can only handle 30 characteristics. Got things working for sending out parameters but often the updating command fails. Don't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
2016-07-27 Added detailed specification for 40 pin main connector from main CPU board to power board in the DMOC645.
2016-07-31 Added a few more data items to BLE data comm. Added state of charge to BatteryManager - no idea why it wasn't already there.
2016-08-02 Added a test throttle and test inverter that can be used to test the new BLE system without actual hardware or can be used for testing. Fixed up some BLE bugs.
2016-08-03 Fixed timeRunning, sped up and reorganized characteristic updates
    [config.h]
2016-09-02 Switch system I/O functionality to a class instead of bare C++ functions. Add ability to register CAN connected I/O into the system.
2016-09-02 Added more advanced CAN handler from ArduinoDue / Private branch. Now can do CANOpen as well. Added PowerKeyPro device driver.
2016-09-11 Changed tick handler and device manager classes to be stack allocated instead for ease of development
2016-09-19 Fixes for CANIO, fixes and clean up for system EEPROM settings, addition of a module to use for vehicle specific code
    [DeviceManager.cpp, SerialConsole.cpp]
2016-09-19 Changes to allow CK Inverter to work with gear and enable status set by rest of code (instead of being hardcoded)
2016-09-19 Switch to only initialize BLE module at first power up and then use the existing configuration from then on.
2016-09-21 Fix automatic ADC compensation
2016-09-21 Add ability to dump device table or reinitialize it. Both for debugging.
2016-09-21 Change text output of device table init to be console instead of debug
2016-09-22 Switched up code to support negative ADC readings (only for GEVCU6). That board has full support for negative readings as well. Switched GEVCU6 ADC to be 13 bit signed which essentially gives it the 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
2016-09-23 Renamed .ino file to match directory name, reformatted output of heartbeat to show throttle status better.
2016-09-23 Change device table dump to use console instead of info logging level
2016-09-23 Serial Console Cleanup
    Tried to rationalize our menu system in Serial Console. I failed. But
    artfully I hope.
    [DeviceManager.cpp, GEVCU6.ino, Heartbeat.cpp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]
2016-09-24 Read me updates
    Updated read me. We can now use Arduino IDE’s later than 1.54.
    Termination is built into the new hardware. The GEVCU6 version only
    supports new 6.23c or later hardware.
2016-09-25 Updated version number, fixed Vehicle Specific so it can be turned on/off now, added missing feedback messages in serial console
    [SerialConsole.cpp, config.h]
2016-09-26 Code change to hopefully alleviate device table resets, zero out parameters over BLE that don't get used.
    [GEVCU6.ino, eeprom_layout.h]
2016-09-28 Many changes to BLE code to make it work more reliably and to allow GATT characteristic writes from a connected device to work.
2016-09-30 Switched from polled mode to callbacks for GATT characteristic changes
2016-10-02 Switch to using a polled state machine for analog setup (shrinks start up time). Also disabled more of fault handler also to save start up time.
2016-10-02 Fixed speed mode on DMOC, sped up I2C comm quite a bit, testing for interrupts with BLE
    [DmocMotorController.cpp, GEVCU6.ino]
2016-10-08 200 rpm torque command modification
    Commented out cancellation of regen for rpm < 200. This is actually
    quite dangerous.
    If brake input is used for regen, you get strong regenerative braking
    for a given pedal input. But as rpm decreases below 200, the regen is
    suddenly released and the car surges forward suddenly - just as you
    slow down to stop before a car in front of you at a stoplight.
2016-10-10 Throttle fixes (allow negatives since this board can generate them), taper regen on DMOC as speed lowers, source code restructuring
    [DmocMotorController.cpp, MotorController.cpp, MotorController.h]
2016-10-10 Small fix to clean up extraneous info messages when throttle is weird
    [PotThrottle.cpp]
2016-10-13 Fixes to make device initialization safer, addition of ability to automatically set up to 6 devices active when initializing for the first time
    [config.h]
2016-10-13 Improved some text output for start up messages, added code to try loading device table three times upon start up - to help with a potential issue where the first time might get corrupted since it is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
    [GEVCU6.ino]
2019-10-09 Fixes to make the Brusa code not brick GEVCU. It's still hard coded though.
    [BrusaMotorController.cpp]

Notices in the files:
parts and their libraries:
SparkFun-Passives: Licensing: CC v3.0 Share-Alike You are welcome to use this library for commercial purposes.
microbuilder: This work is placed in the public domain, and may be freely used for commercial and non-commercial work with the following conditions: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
